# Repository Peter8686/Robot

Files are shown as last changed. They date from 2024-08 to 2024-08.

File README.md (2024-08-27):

# Ứng dụng cảm biến quang trở trong dò đường cho Robot

## Intro

Đầu tiên, đây là 1 dự án miễn phí nhằm hỗ trợ các bạn học viên, sinh viên áp dụng công nghệ dò đường cho robot sử dụng cảm biến quang trở.

Công nghệ dò đường cho robot sử dụng các cảm biến quang trở hay hồng ngoại,...v.v đã có từ rất lâu. Tuy nhiên để có thể áp dụng một cách hiệu quả, lựa chọn được cảm biến có độ ổn định và chính xác cao thì đối với các bạn học viên, sinh viên có thể còn gặp nhiều khó khăn.

## Nguyên lý hoạt động của quang trở và ứng dụng trong dò đường robot

Quang trở là 1 cảm biến thay đổi giá trị điện trở theo cường độ ánh sáng chiếu vào nó. Cường độ ánh sáng càng mạnh thì điện trở của quang trở càng nhỏ và ngược lại.

Ánh sáng chiếu vào các màu sắc khác nhau sẽ bị hấp thụ 1 phần khác nhau, còn lại là chúng phản xạ trở lại dẫn đến cường độ ánh sáng phản xạ trở lại là khác nhau. Các robot dò đường thường có những đường "line" để đi theo. Và màu sắc của các đường "line" sẽ khác biệt với màu nền. Giả sử trong các sân chơi robot, màu "line" sẽ là màu trắng, màu nền sân là màu xanh lá. Nếu dùng 1 đèn led chiếu vào "line" và màu nền sân, để cảm biến quang trở gần đó thu lại ánh sáng phản xạ từ "line" và nền sân, ta sẽ thấy giá trị điện trở của quang trở sẽ có sự khác biệt, chính là bởi vì ánh sáng phản xạ của "line" và màu nền sân là khác nhau. Dựa vào nguyên lý như vậy, ta có thể áp dụng quang trở để phân biệt "line" và nền sân.

<div align="center">
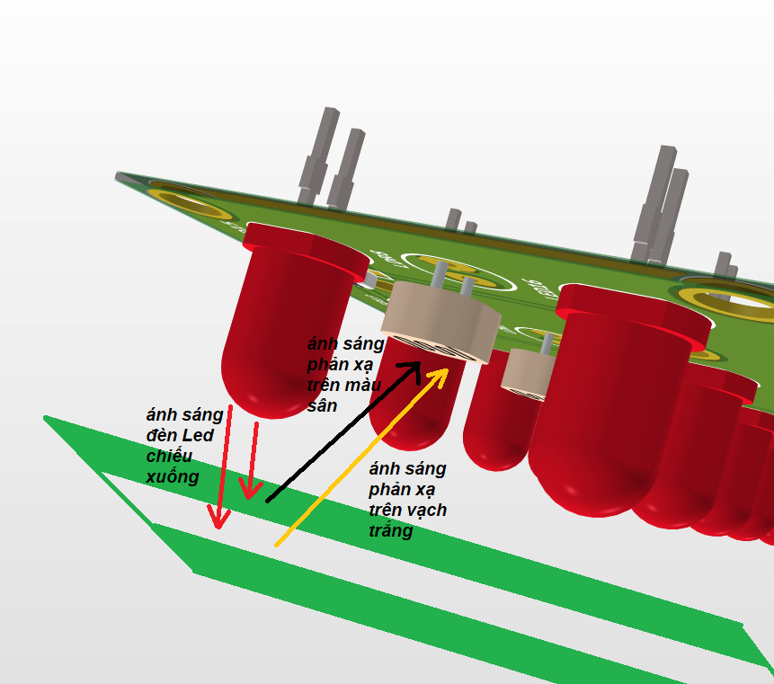
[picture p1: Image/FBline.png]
Schematic
    
</div>

<div align="center">
    <p>Mô tả thực tế</p>
</div>

## Từ sự thay đổi về điện trở của quang trở, làm thế nào để vi điều khiển biết được?

Bằng cách mắc mạch theo kiểu cầu phân áp dưới đây, ta cấp cho cầu phân áp điện áp tham chiếu VREF, khi quang trở LDR9 có sự thay đổi về điện trở, điện áp rơi (ADCIN) trên quang trở cũng sẽ thay đổi theo. Đưa giá trị điện áp này vào ngoại vi ADC của vi điều khiển, chúng ta sẽ xác định được giá trị này.

<div align="center">
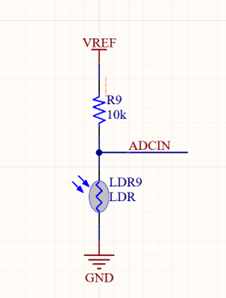
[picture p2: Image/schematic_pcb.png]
Schematic_pcb
    
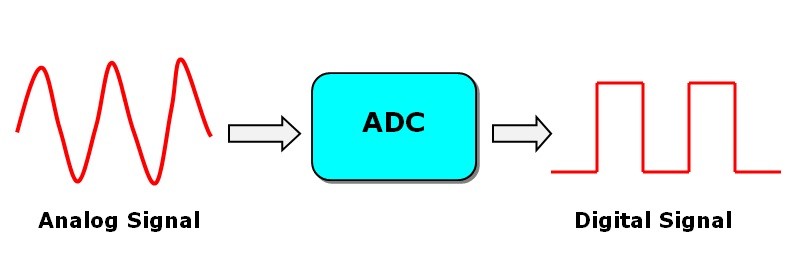
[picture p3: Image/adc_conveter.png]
adcImage
    
</div>

## Thiết kế dàn cảm biến quang trở và led chiếu sáng

Mỗi một cảm biến quang trở, mình sử dụng 2 đèn led để chiếu sáng. Mục đích là để tăng cường độ ánh sáng chiếu và ánh sáng phản xạ. Bởi nếu ánh sáng chiếu yếu, khi gặp các nguồn sáng mạnh hơn từ môi trường chiếu vào sẽ làm nhiễu cảm biến.

<div align="center">
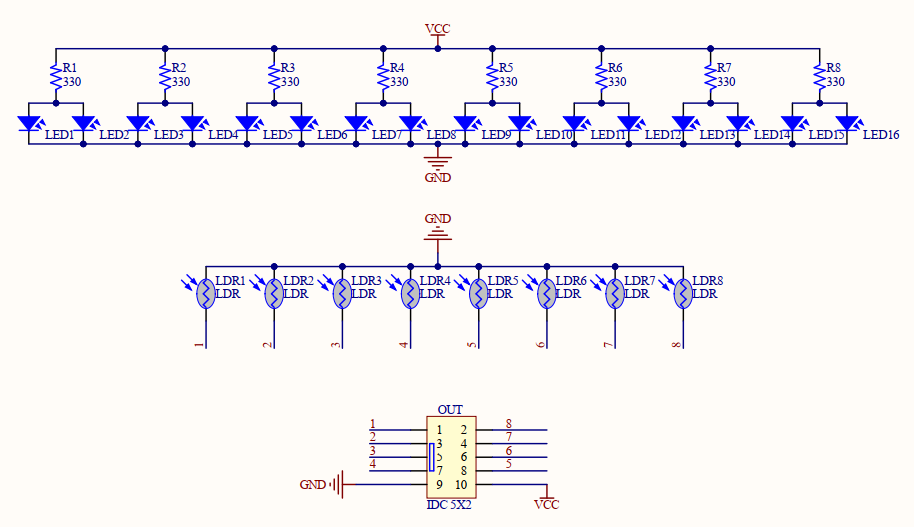
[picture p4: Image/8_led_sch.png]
8ledSchematic
    
</div>

<div align="center">
    <p>Sơ đồ nguyên lý dàn cảm biến quang trở và led chiếu sáng</p>
</div>

Led và quang trở được bố trí như ở dưới đây, chỉ lưu ý khoảng cách giữa 2 cặp led và quang trở ở giữa nên được thay đổi khi độ rộng đường line thay đổi. Ví dụ độ rộng đường line là 3cm thì 2 cặp led và quang trở ở giữa các bạn nên để khoảng cách khoảng 2.8cm, để 2 cặp led và quang trở này nằm ở giữa vạch khi robot chạy giữa line.

<div align="center">
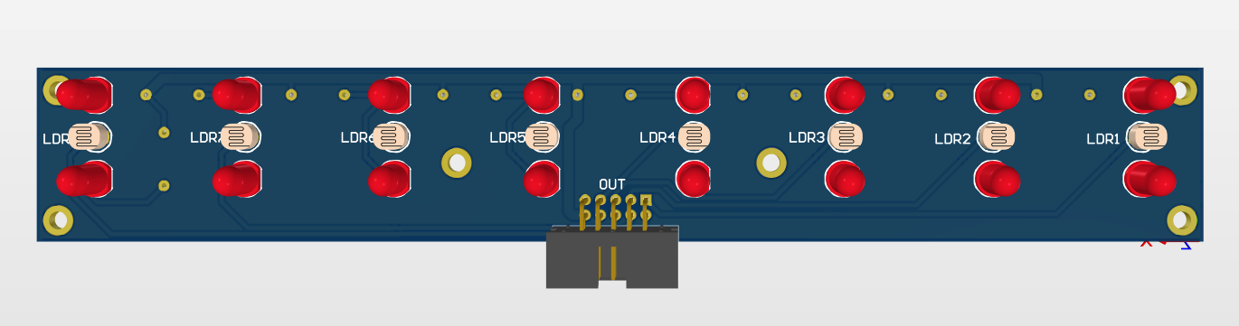
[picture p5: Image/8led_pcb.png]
8ledpcb
    
</div>

<div align="center">
    <p>Mạch in dàn cảm biến quang trở và led chiếu sáng</p>
</div>

Mạch in mình thiết kế là 2 lớp, các bạn có thể đặt mạch trực tiếp từ [Jlcpcb.com](jlcpcb.com). Các bạn cần có thẻ Visa để thanh toán và đặt hàng.

<div align="center">
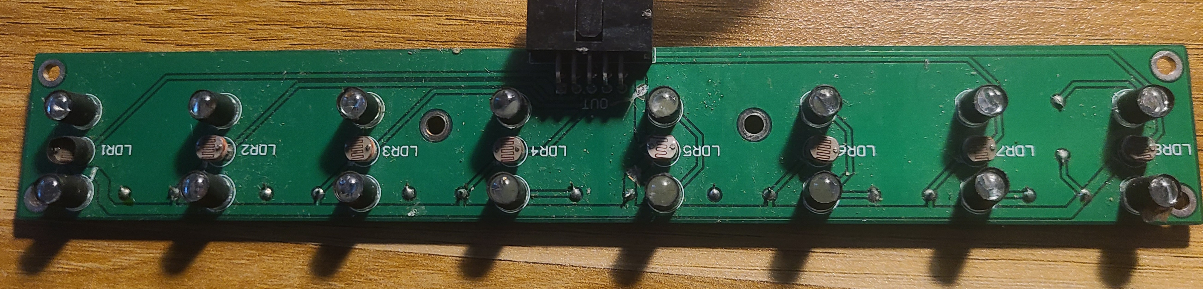
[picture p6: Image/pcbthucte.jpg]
8ledpcbtt
    
</div>

<div align="center">
    <p>Mạch thực tế dàn cảm biến quang trở và led chiếu sáng</p>
</div>

Các bạn nên thiết kế thêm phần ngăn cách giữa các led và với bên ngoài môi trường để giảm sự ảnh hưởng bởi ánh sáng môi trường và ánh sáng của led bên cạnh gây nhiễu cảm biến. Mình đã thiết kế phần ngăn cách, in 3d và lắp ráp vào dàn cảm biến như thế này:

<div align="center">
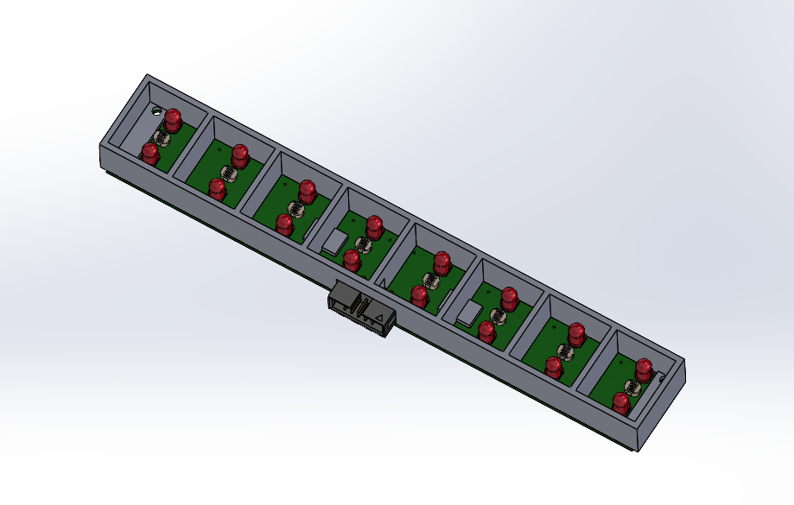
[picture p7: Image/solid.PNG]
solid
    
</div>

<div align="center">
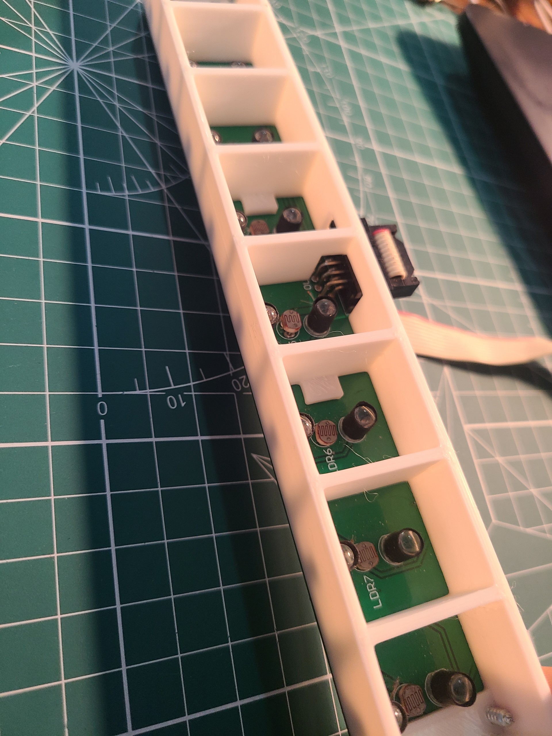
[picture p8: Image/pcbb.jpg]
pcbb
    
</div>

<div align="center">
    <p>Khối ngăn cách cảm biến</p>
</div>

Mời các bạn xem phần [Thiết kế mô đun xử lý tín hiệu cho dàn cảm biến quang trở và led chiếu sáng](https://github.com/Peter8686/Robot_ADCModule.git) để kết hợp 2 mô đun lại và biết cách sử dụng.

#### Mọi thắc mắc xin liên hệ qua địa chỉ email của tôi: thaohv1639x@gmail.com 
## Thanks for watching!

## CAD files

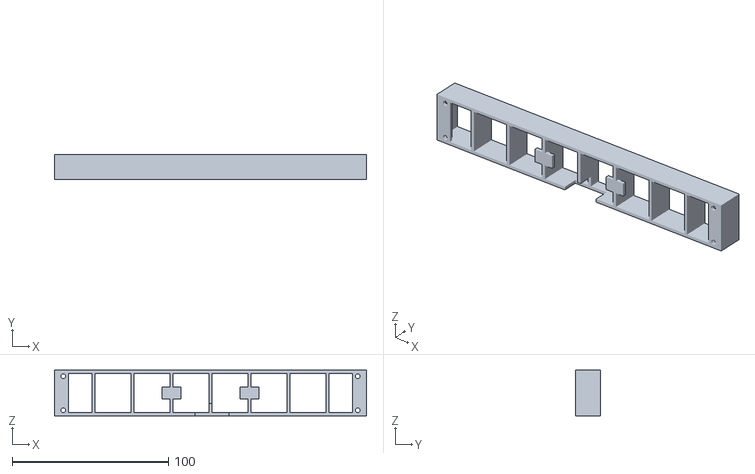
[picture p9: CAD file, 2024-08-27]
3Dprinter/Chan led.STL
200.0 x 16.0 x 29.2
